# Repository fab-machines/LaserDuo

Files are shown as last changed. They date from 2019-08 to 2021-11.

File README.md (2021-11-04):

<div align="center"><h1 style="font-family: courier;" align="center">LaserDuo</h1></div>

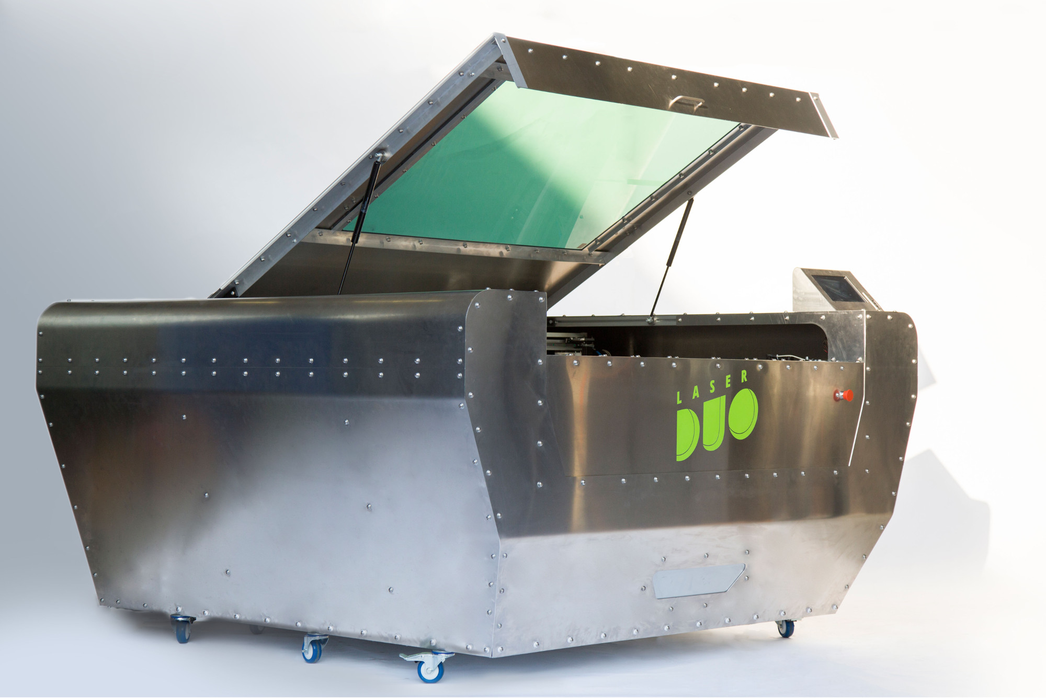
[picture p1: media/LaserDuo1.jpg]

<div align="center"><i>Open Source Dual Laser Cutter</i></div>

Premises
--
We dream in a future of freedom, where open source hardware and [Fab Labs](https://fablabs.io/) enable people to fully understand how to make things they need, and where decentralized local production is customized to impact the surrounding community. Believing that empowering the user with knowledge about how to make machines, LaserDuo wants to give to the world a powerful open source tool, to lasercut (almost) any material. And, together with [BigFDM](https://github.com/fab-machines/BigFDM), this is one of the first steps in developing other machines sharing the same philosophy.

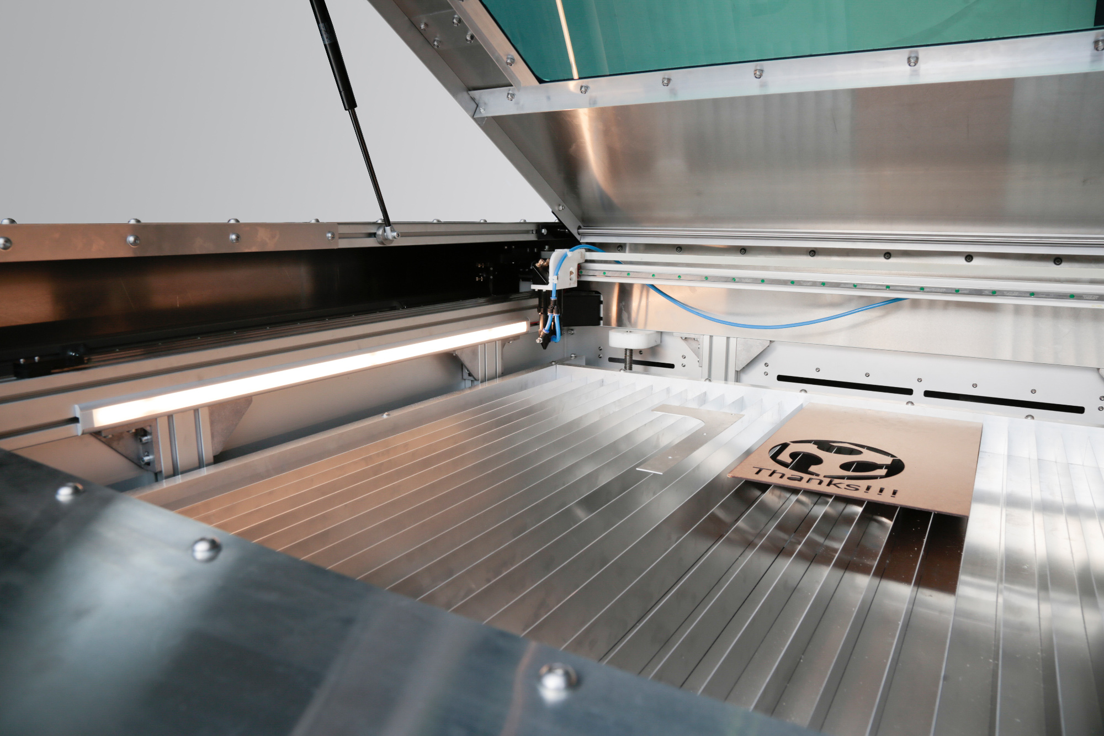
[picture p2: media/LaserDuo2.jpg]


LaserDuo
--
LaserDuo is an open source laser cutter having two different laser sources. Using a 130W CO2 and a 75W YAG lasers, LaserDuo can work with a wide range of materials such as wood and metals.

Taking advantage of what we have learned in [Fab Academy](https://fabacademy.org/), LaserDuo has been developed using standard [Fab Lab equipment](https://docs.google.com/spreadsheets/d/1U-jcBWOJEjBT5A0N84IUubtcHKMEMtndQPLCkZCkVsU/pub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) and [techniques](http://fab.academany.org/2019/schedule.html) plus a membrane press machine to bend the aluminum parts. LaserDuo was developed at [Fab Lab Kamp-Linfort](https://fablab.hochschule-rhein-waal.de/about-us) by Daniele Ingrassia. Reversing the consumer process, where knowledge and building of machines stays inside a black box managed by companies, LaserDuo brings the advantages of an open source development:

- full awareness about how the machine works
- reproducible design
- possibility to customize the machine and/or to build new ones
- built as much as possible with local materials
- local self-fixing and self-production of the machine parts
- community can use and improve the design
- cheap alternative to large scale 3D printers
- use LaserDuo as tool to produce other open source machines

Developed and built in a Fab Lab as multipurpose machine, LaserDuo allows to access the laser cutting technology at lower price in comparison to similar machines available on the market. Especially considering the possibility to work with metals. The open source design allows the user to fix the machine by himself, and to be aware of the process in a way that he can use it to reproduce the machine or parts for it. Being a challenging project from several aspects, such as size of the working area, Z-axis, speed, resolution and the dual laser, it also offers additional features like an integrated PC to control the machine and launch jobs, air assist, solid aluminum bodywork.

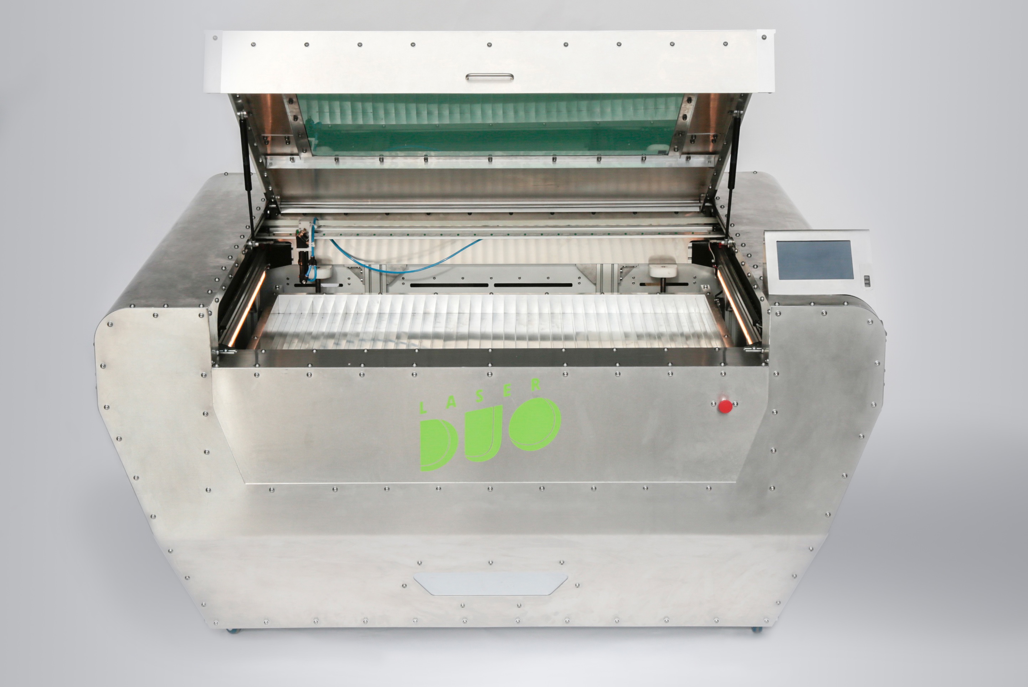
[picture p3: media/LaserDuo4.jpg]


**LaserDuo specifications**:

- **1500mm x 1000mm** cutting area
- **500mm Z axis**
- **dual laser source**
- **130W CO2** laser
- **75W YAG** laser
- **800mm/s** maximum speed
- **Nema 24** stepper motors
- **air assist**
- integrated **tablet** for machine control
- **1000DPI or 0.0254mm** resolution
- open source **satshakit biards** for machine control
- dedicated sealed **exhaust chamber**
- **certified laser protective window**
- **safety features** emergency switch, windows interlock
- **fully enclosed 100% aluminum housing**
- dimensions: 2250mm x 2100mm x 1500mm

Machine design
--
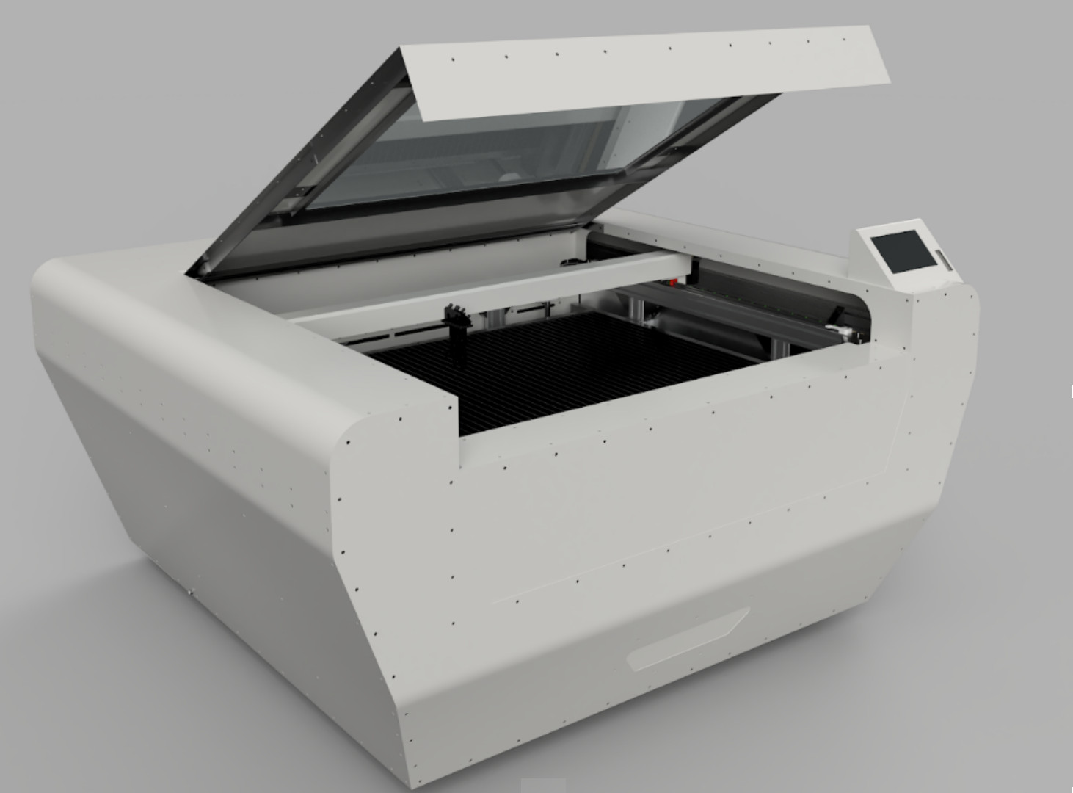
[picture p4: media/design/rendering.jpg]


The overall project has been designed by following a bottom-up approach, where the first step was to make a single machine axis. Every step focused on developing a single machine section, designing and constraining it according to the previous steps and machine features. You can consider this like being almost blind about the next step, until the current one has been assessed as able to work properly. It is therefore for me still astonishing the complete transition to the final machine look, generated by the chaining of the dependencies of several design steps.

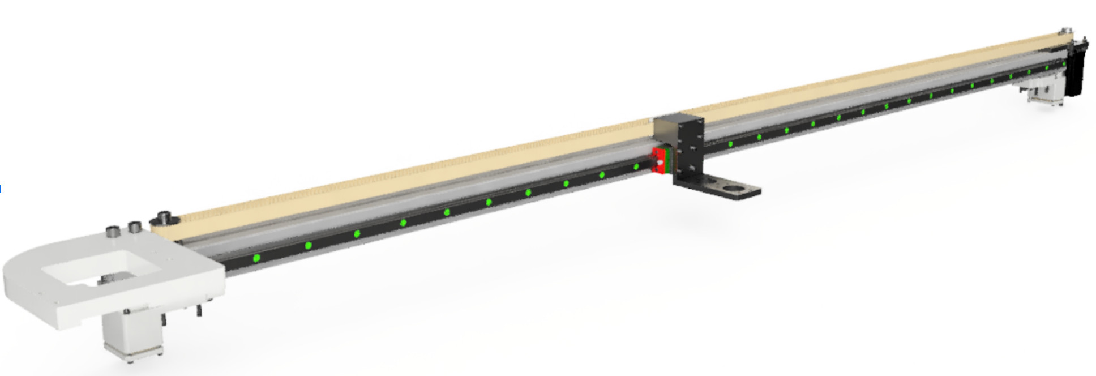
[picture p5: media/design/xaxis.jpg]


X and Y stages
--

As many other laser cutters, also the stages of LaserDuo have been designed to be light and fast. Linear rails together with CNC milled POM and aluminium profiles have been used. To be noticed this step took a lot time, especially during the assembly to ensure the correct squareness of the frame and the perpendicularity of the axis. Both X and Y axis are moved by Nema 24 motors.

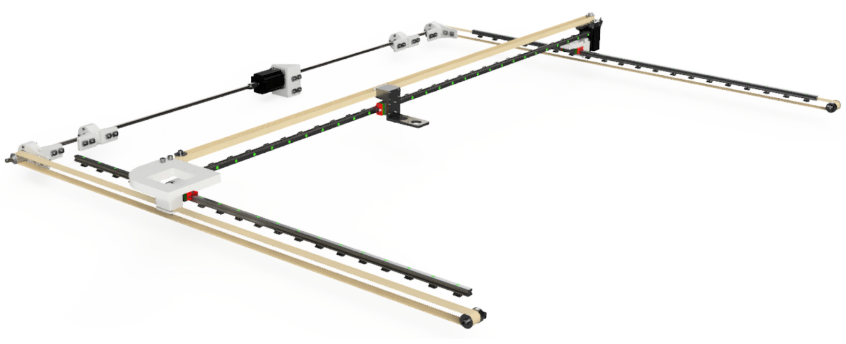
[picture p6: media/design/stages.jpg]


Z Axis
--

I always had something to do with lasers having Z axis, before learning that some chinese laser don’t have it. Therefore for me was quite normal to consider to have it. However I had a long reasoning about the justification of the extra costs vs the possible benefits. Then I had the idea to eventually make a 3D printer as a possible upgrade for LaserDuo, while considering that I still needed to find a solution to properly take the focus by moving the lens up and down. That convinced me to add it. The Z axis consist of 4 lead-screws, supported by ball bearings and moved a closed loop belt. The frame has been designed in a way to fit the Z axis inside and to have the machine high enough to be on wheels.

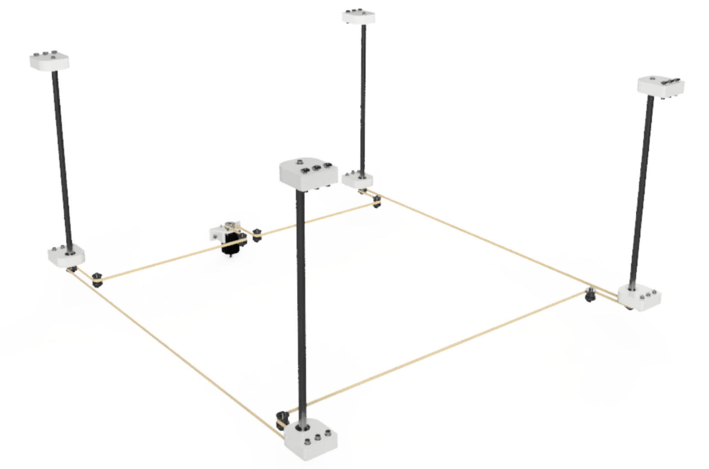
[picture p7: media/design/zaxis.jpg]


Inner enclousure
--

Designed on purpose to shield the laser focusing area and to make the fumes having a certain flow towards the exhaust system, the inner enclosure consists of CNC milled 1.5mm anodized aluminium sheets. There are vents both in the front and the back, allowing fresh air to come from outside, cool the cutting area, and be exhausted through a sealed box.

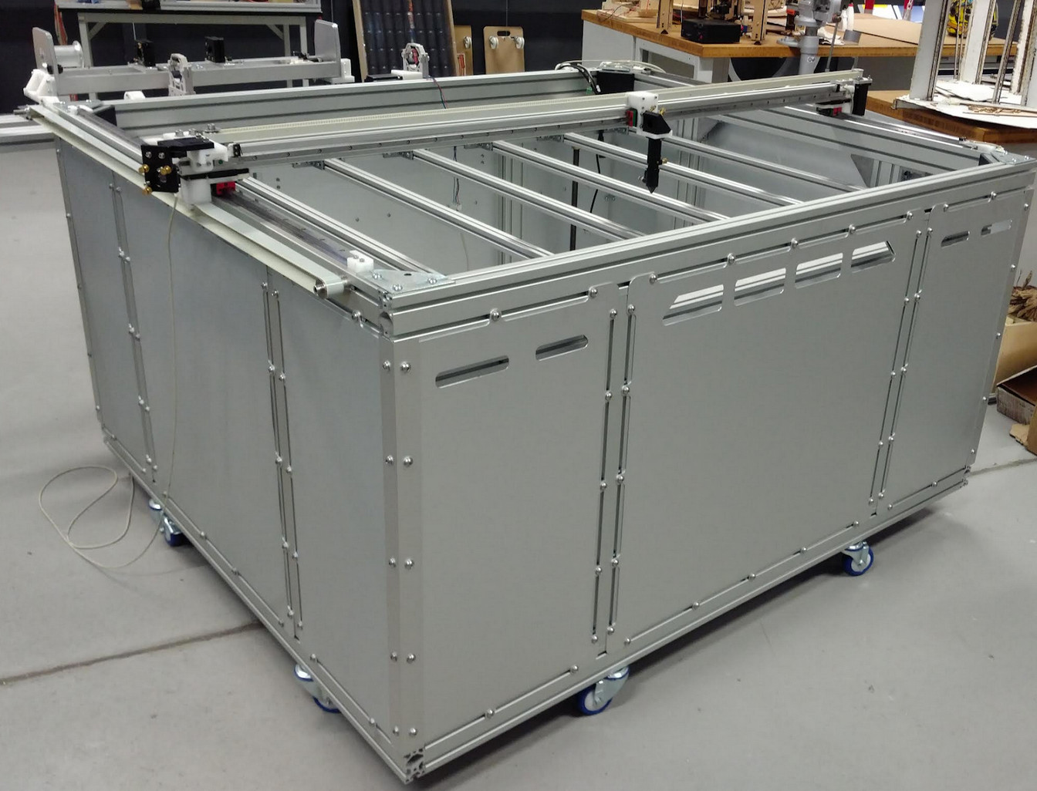
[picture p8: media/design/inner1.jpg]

<br><br><br>
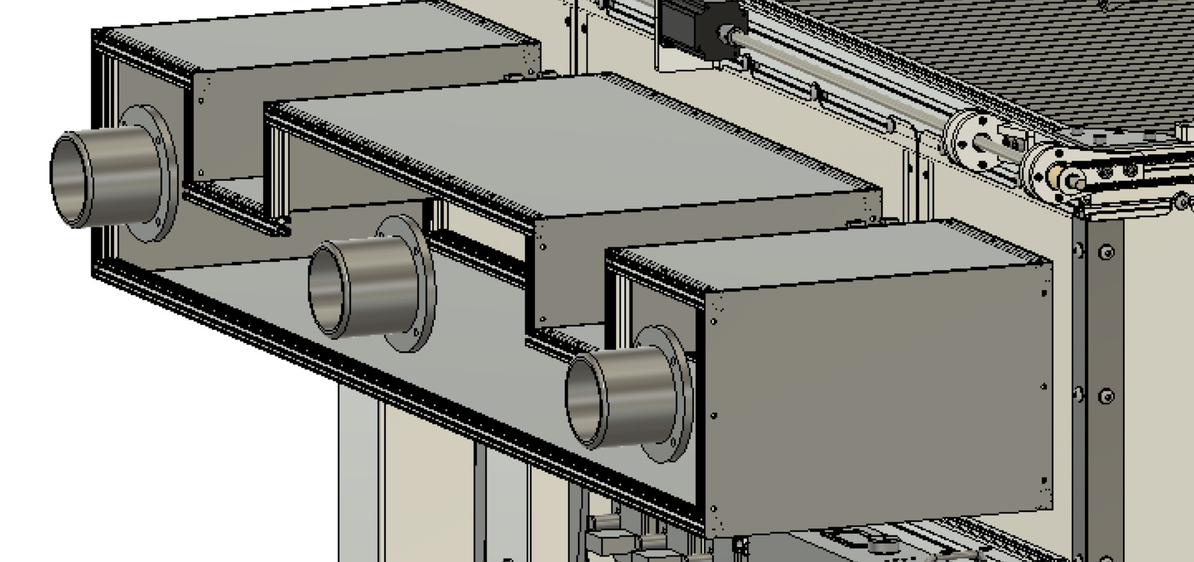
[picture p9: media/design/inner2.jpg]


Housing
--

The housing completely encloses the machine, while keeping 3 exhaust tubes in the back and some ultrathin air intakes. The design uses curves to allow the feet to fit when coming close to the machine, and as well to save material. Laser, exhaust, electronics and optics are located in different areas, accessible by removing a specific panel for maintenance.

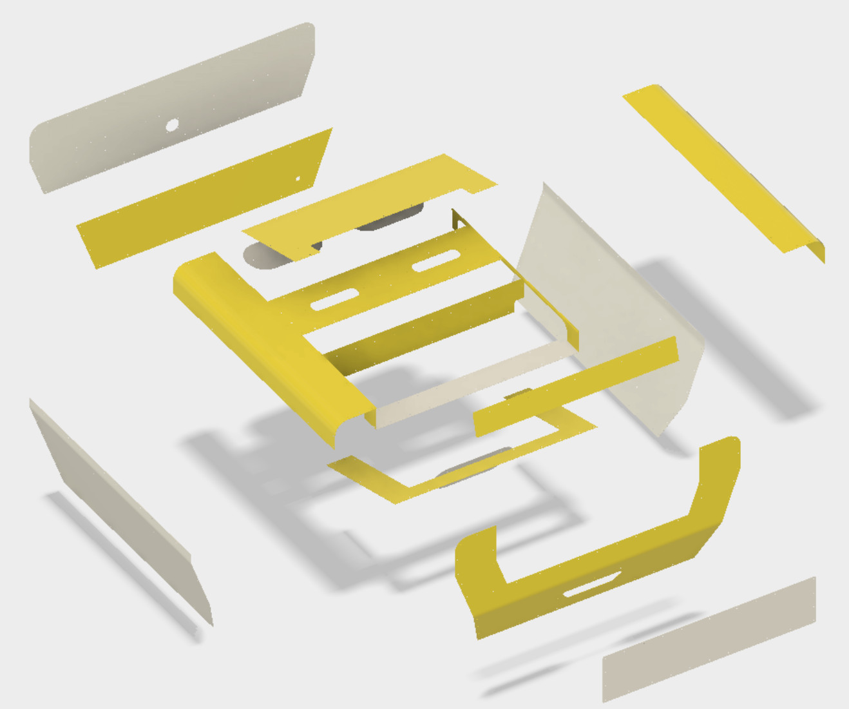
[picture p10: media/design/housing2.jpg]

<br><br><br>
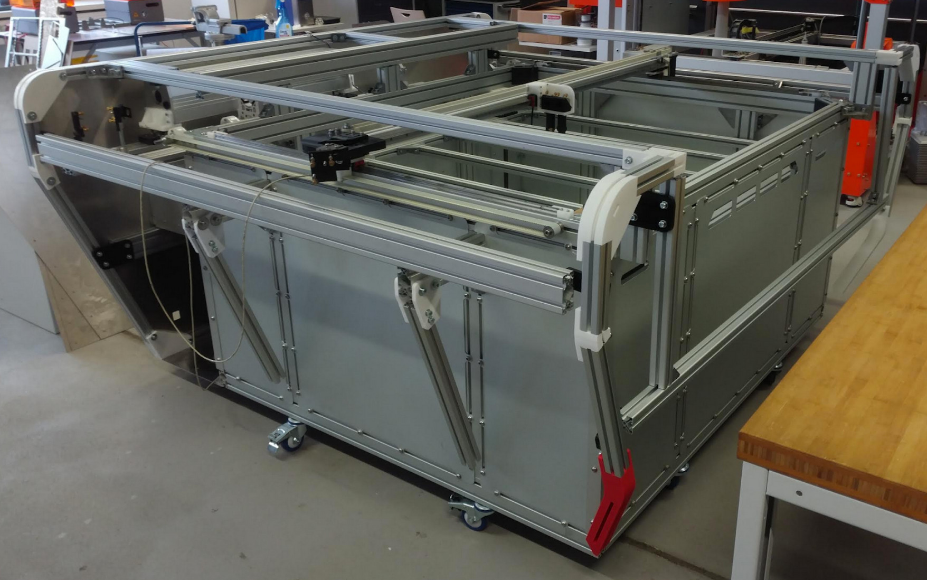
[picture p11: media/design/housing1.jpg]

<br><br><br>
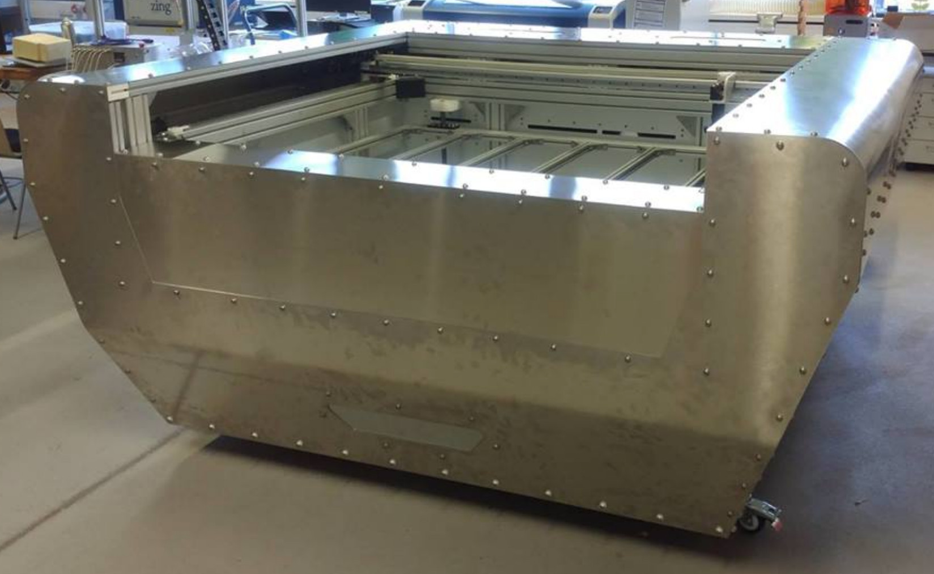
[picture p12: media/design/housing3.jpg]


Electronics
--
The electronics of LaserDuo consists of a set of fabbable electronics, derived from the original **[satshakit](https://github.com/satshakit)** board and **[satstep](https://github.com/satstep)** stepper drivers. Following the used boards and their role in LaserDuo.<br>

**[satshakit-mega](https://github.com/fab-machines/LaserDuo/tree/master/electronics/satshakit-mega)**

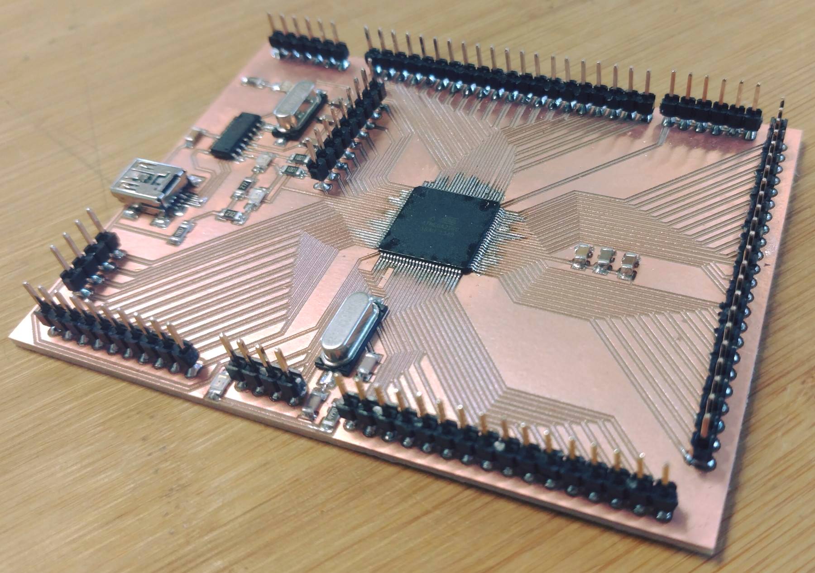
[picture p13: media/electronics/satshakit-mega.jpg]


Based on the [ATMega2560](https://www.microchip.com/wwwproducts/en/ATmega2560), this board provides the necessary microcontroller hardware to manage LaserDuo dual laser logic and additional sensors. Furthermore integrates an USB-to-Serial converter and USB port. Developed as general purpose board, not all the pins will be used. In the future this board will be a custom made solution for LaserDuo. Link to the original [repo](https://github.com/satshakit/satshakit-mega).

---------

**[satshakit-grbl](https://github.com/fab-machines/LaserDuo/tree/master/electronics/satshakit-grbl)**

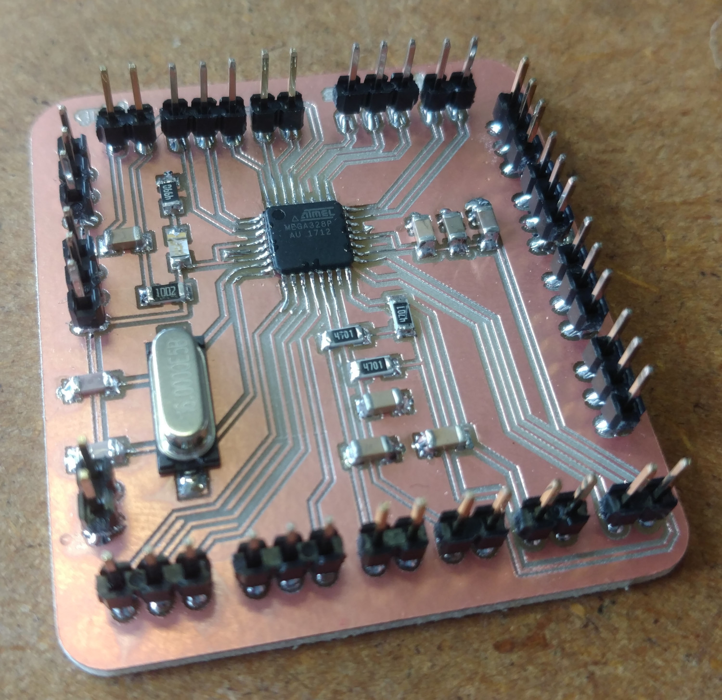
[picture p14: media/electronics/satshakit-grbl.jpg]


Used to run **[GRBL 1.1](https://github.com/gnea/grbl)** in laser mode, satshakit-grbl is based on the ATMega328p and as well integrates nise filtering for the endstops. Link to the original repo [satshakit-grbl](https://github.com/satshakit/satshakit-grbl)

---------

**[satstep6600](https://github.com/fab-machines/LaserDuo/tree/master/electronics/satstep6600)**

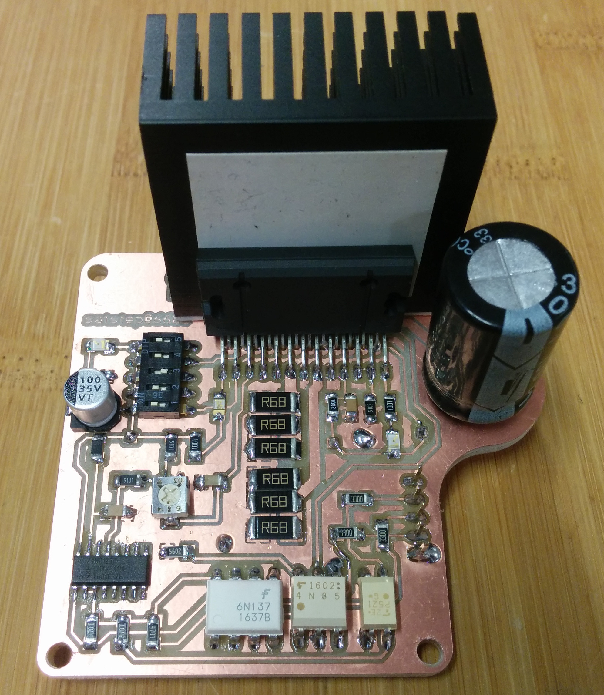
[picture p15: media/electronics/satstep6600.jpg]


Proved to have a robust design by being used in **[LaserDuo](http://laserduo.com/)** for more than a year, the satstep6600 is the stepper driver used to move the NEMA 24. Based on the Toshiba [TB6600HG](http://www.massmind.org/images/massmind/TB6600HG_datasheet.pdf) it can give up to 4.5A per coil to a single motor, whereas the NEMA 24 used will take a maximum of 4A. Link to the original [repo](https://github.com/satstep/satstep6600).

---------

Summary of the needed boards:

- 1 x satshakit-mega
- 1 x satshakit-grbl
- 3 x satstep6600

To power all this electronics, and to control the laser sources the following additional electronics is needed:

- 15A 24V power supply
- CO2 power supply (~40KV)
- YAG power supply

Make your own LaserDuo
--

LaserDuo is made by using a mix of fabricated and ready-made parts. The ready-made parts are selected to be as common/standard as possible, to make the sourcing of them easy in many countries. For both the raw materials needed for the fabricated parts, and the ready-made parts, refer to the Bill-of-Material for details: **[LaserDuo BOM](https://github.com/fab-machines/LaserDuo/raw/master/docs/LaserDuo%20BOM.pdf)**

The fabrication of the parts mainly relays on standard [Fab Lab equipment](https://docs.google.com/spreadsheets/d/1U-jcBWOJEjBT5A0N84IUubtcHKMEMtndQPLCkZCkVsU/pub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) plus a membrane press machine. Below a list of the required tools and machines:

- C02 laser cutter:
 - able to cut 8mm POM
 - needed for POM parts and holders
- large format wood CNC machine:
 - ShopBot or similar, size 2500x1250mm
 - to machine the POM parts (X, Y, Z, axis)
 - to machine the Aluminum parts (inner enclousure, housing)
- 3D printer:
 - a medium sized one (50x50x50cm)
 - to print the inner housing parts 
- Desktop format CNC machine:
 - Roland MDX50/MDX20/SRM20 or similar small machine (as well the cheap chinese ones)
 - to produce the required PCBs
- standard set of tools:
 - spanner key set
 - hex key set
 - DIN 875
 - calipers
 - rulers
 - screwdriver set
 - player set (grabber/cutter etc..)
 - clamps
 - rubber hummers
- membrane press machine
 - to bend the housing parts  

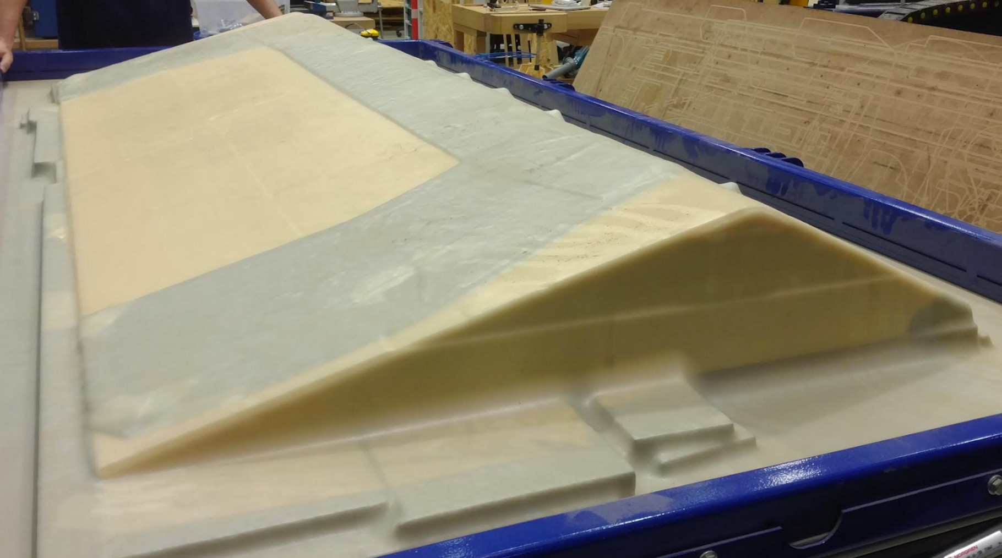
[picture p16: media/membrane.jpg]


Both fabricated and ready-made parts have been modeled inside the **[LaserDuo Fusion 360 3D model](https://github.com/fab-machines/LaserDuo/raw/master/cad/LaserDuo.f3d)**. Using Fusion is possible to export/prepare the parts for production in the following ways:

- right click save as STL, on a body that needs to be 3D printed
- use the built-in Fusion CAM processor for the machined parts
- project on a surface, and then right click export as DXF, for laser cutting
 
For more details about the tools and once you have all the fabricated and ready-made parts parts available, refer to the for step-by-step assembly instructions and tips: **[LaserDuo Building Manual](https://github.com/fab-machines/LaserDuo/raw/master/docs/LaserDuo%20building%20manual.pdf)** 

LaserDuo requires different fabbable PCBs to work. Below the download links for the eagle files that you use to fabricate them:

- **[satshakit-mega schematic](https://raw.githubusercontent.com/fab-machines/LaserDuo/master/electronics/satshakit-mega/satshakit-mega.sch)**, **[satshakit-mega board](https://raw.githubusercontent.com/fab-machines/LaserDuo/master/electronics/satshakit-mega/satshakit-mega.brd)**

- **[satstep6600 schematic](https://github.com/fab-machines/LaserDuo/raw/master/electronics/satstep6600/satstep6600.sch)**, **[satstep6600 board](https://github.com/fab-machines/LaserDuo/raw/master/electronics/satstep6600/satstep6600.brd)**

- **[satshakit-grbl schematic](https://github.com/fab-machines/LaserDuo/raw/master/electronics/satshakit-grbl/satshakit-grbl.sch)**, **[satshakit-grbl board](https://github.com/fab-machines/LaserDuo/raw/master/electronics/satshakit-grbl/satshakit-grbl.brd)**

Media
--
**LaserDuo Videos**

<a href="http://www.youtube.com/watch?feature=player_embedded&v=9PNHiuEieJk
" target="_blank"></a>

<a href="http://www.youtube.com/watch?feature=player_embedded&v=rJKmr8BXJXA
" target="_blank"></a>

<a href="http://www.youtube.com/watch?feature=player_embedded&v=EAzdC5dfosA
" target="_blank"></a>

**How to Make LaserDuo: Hamburg Workshop at [Open Lab](http://openlab-hamburg.de/startpage/)**

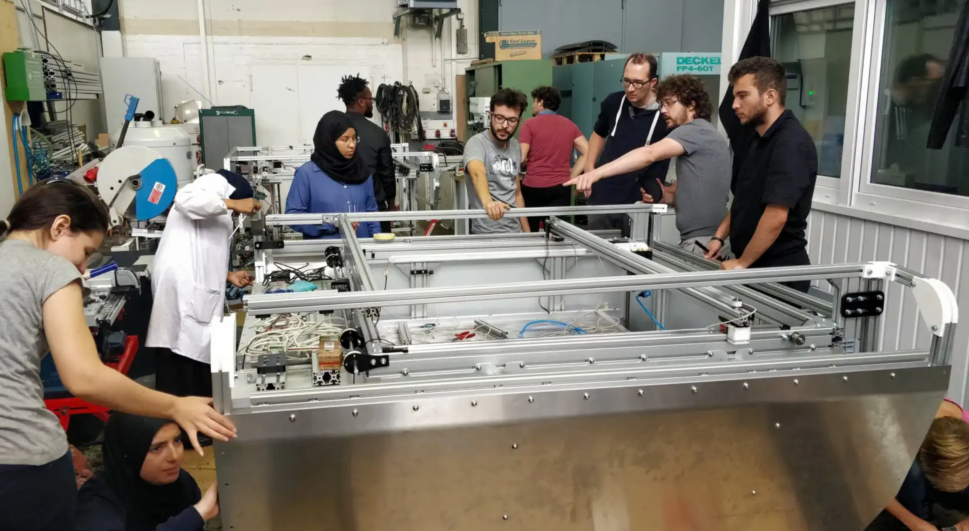
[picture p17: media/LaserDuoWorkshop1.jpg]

<br><br><br>
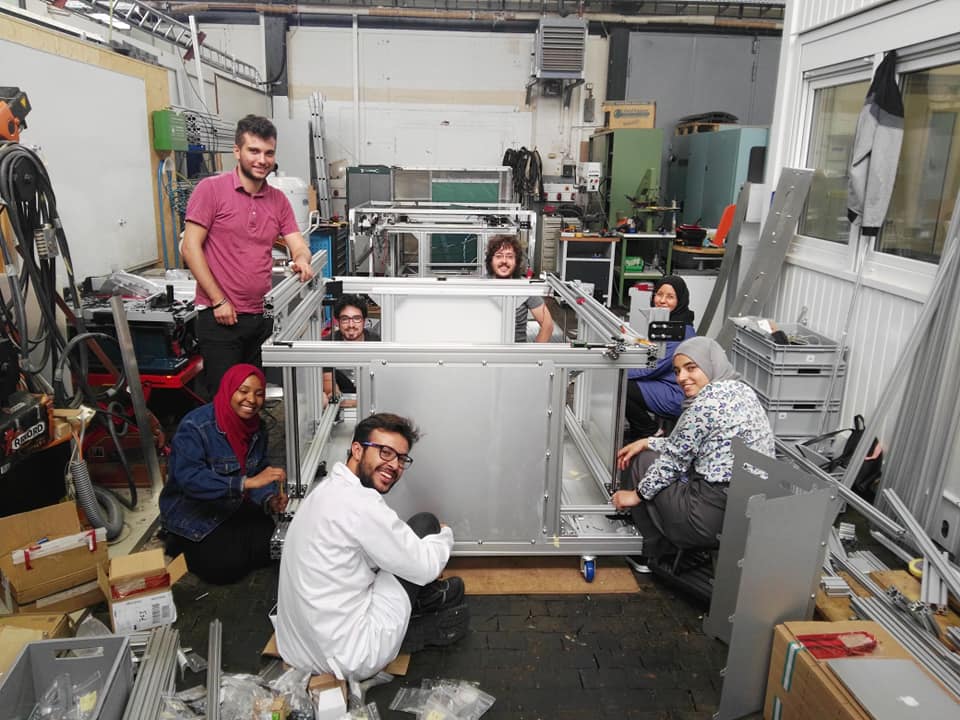
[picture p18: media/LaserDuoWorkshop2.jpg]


**LaserDuo pictures**

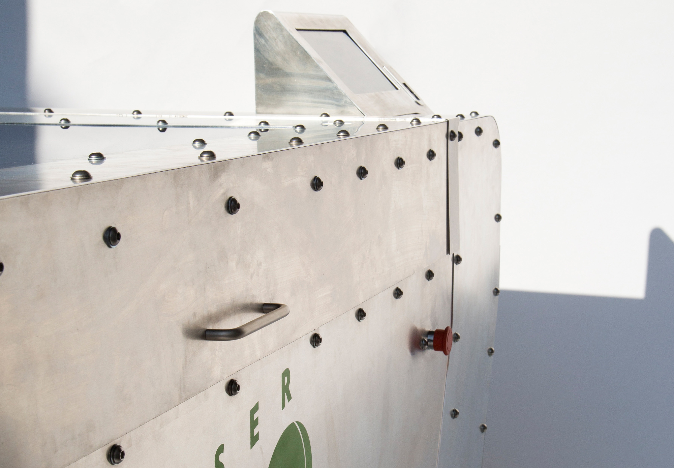
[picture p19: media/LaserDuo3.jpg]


Author
--

The author of BigFDM is:

- **Daniele Ingrassia, daniele@inmachines.net**
- **[InMachines Ingrassia GmbH](https://www.inmachines.net/)**

Donations
--

Our dream is to have impact by making **open source machines digitally available and locally produced anywhere in world**. We plan to open a dedicated Fab Lab to foster open machine building and digital fabrication research. Practically several tasks and many expensens have to be sustained to give this dream the chance to have a future. Such as the renting of a proper space, the making/purchasing of proper equipment, the sustainability of our work and lifes. If you share this mindset and BigFDM is useful to you, please help us to make this dream a reality by donating your support:



Acknowledgements
--

**Thanks:**<br>
<br>
**[Fablab Kamp-Lintfort](https://fablab.hochschule-rhein-waal.de/)**<br />
Hochschule Rhein-Waal<br/>
Friedrich-Heinrich-Allee 25<br/>
47475 Kamp-Lintfort - Germany<br/>
[https://fablab.hochschule-rhein-waal.de/about-us](https://fablab.hochschule-rhein-waal.de/about-us)<br/>
[fablab@hochschule-rhein-waal.de](fablab@hochschule-rhein-waal.de)

Technical Help by **[Ahmed B. Abdellatif](http://archive.fabacademy.org/fabacademy2017/fablabkamplintfort/students/391/index.html)**<br/>
Logo Design by **Jana-Lina Berkenbusch**<br/>
Photographs by **Christian Spieß**<br/>
Website development by **Emir Rustamov**<br/>

****

License
-- 
LaserDuo, its hardware design, CAD, BOM, settings and relative files are are released under the following open source license:

- CERN Open Hardware Licence Version 2 Weakly Reciprocal - **[CERN-OHL-W](LICENSE_CERN_OHL_W_V2.txt)**

Note
--

This documentation will be continuously improved as soon there are updates and/or improvements on the machine.

Disclaimer  
--

<div class="align-justify">
This hardware/software is provided "as is", and you use the hardware/software at your own risk. Under no circumstances shall any author be liable for direct, indirect, special, incidental, or consequential damages resulting from the use, misuse, or inability to use this hardware/software, even if the authors have been advised of the possibility of such damages.</div>

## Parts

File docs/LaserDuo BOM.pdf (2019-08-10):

NOTE: all the costs are in euro, and they include VAT, shipping costs and/or eventually importing taxes for Germany. The costs are approximate and can be subject to changes due to variations of currency exchange rates, quotes from the companies and market availability at the moment of ordering.

Item | Description | Amount | Vendor | Cost per unit | Total cost: | Note
ZS-1450 laser tube | 100W C02 laser source | 1 | EFR Laser | 284€ | 355€ | total cost is with importing taxes included
ES-100 power adapter | C02 power supply | 1 | EFR Laser | 130€ | 162€ | total cost is with importing taxes included
75W DPL-75 laser module | 75W Yag laser source | 1 | Super Laser | 700€ | 875€ | total cost is with importing taxes included
I20N DPL power adapter | Yag power supply | 1 | Super Laser | 150€ | 190€ | total cost is with importing taxes included
CW5200 Double Head | Water Chiller | 1 | Teyuchiller | 400€ | 500€ | total cost is with importing taxes included
QSD7527 Q-Driver | Q-Switch power adapter | 1 | CETC | 400€ | 500€ | total cost is with importing taxes included
QSGSU-5 Q-Switch | Yag Q-Switch | 1 | CETC | 300€ | 375€ | total cost is with importing taxes included
HGR15 | Linear guides for X,Y | 5mt | Hiwin | 50€ | 250€
T20 lead screws and bras nuts | 20mm pitch lead screws and nuts for the Z axis | 4 x 1.5mt,4 x nuts | Dold-Mechatronics | 50€ | 200€
Pulleys T5 20mm, 16mm and 10mm | Pulleys for X, Y, Z axis | 2x20mm,1x16mm,1x10mm | Generic | 15€ | 60€
Belt T5 20mm, 16mm and 10mm | T5 belts for X,Y,Z axis | 20mm, 16mm, 10mm,15mt | Generic | - | 200€
Nema24 stepper motors | Motors for the X,Y,Z axis | 3 | Generic | 30€ | 90€
satshakit-mega | Main controller | 1 | open source electronics | 15€ | 15€
satshakit-grbl | Secondary controller | 2 | open source electronics | 10€ | 20€
satstep6600 | Stepper driver | 3 | open source electronics | 15€ | 45€
24V 15A power supply | Power supply for the steppers | 1 | Generic | 30€ | 30€
20x20, 40x40, 40x80, 30x30, 30x60 Bosch, L profiles | Aluminium profiles for the frame and the housing | approx 50mt summing all the sizes | Generic | 1,800€ | 1,800€
DIN 912, ISO 7380, DIN 125, DIN 985, DIN 934, Nut8 M4, Nut8 M8, Nut5 M5, Connectors | Screws, nuts and connectors. | - | Generic | - | 400€
608, 628, 638 | Ball bearings for the X,Y,Z axis | 40 | Generic | 2€ | 80€
PLA | PLA for the printed parts | 10Kg | Generic | 14€ | 140€
POM/Derlin | CNC machines POM for mechanical parts | about 70Kg | Generic | 5€ | 350€
Laser optics, head, laser path, lenses | Laser accessory for C02 and Yag | - | Generic | 250€ | 315€ | total cost is with importing taxes included
P1P12 Filter 6mm | Certified laser protective window | 1200mmx900mm | Laservision | 1,800€ | 1,800€
1.5mm anodized aluminium sheets | Aluminium sheets for the internal enclosure | Approx 10 sqm | Generic | 35€ | 350€
1.5mm aluminium sheets | Aluminium sheets for the external enclosure | Approx 16sqm | Generic | 35€ | 560€
Hi10 tablet | Tablet for controlling the machine | 1 | Chuwi | 150€ | 150€
Emergency switches, endstop switches, main switch | Switches for different purposes | 10 | Generic | - | 50€
2X1, 4X1, power cables, signal cables | Shielded electrical cables | 50mt | Generic | - | 100€
Led lights 20W | Wheels to move the machine Plastic water and ir tubes Led lights for the interior | 20mt 20 8 | Generic Generic Generic | 10€ 2€ - | 40€ Water and air tubes 50€ Wheels 100KG M8 Bosch 80€
Air compressor 6 bar 4 cylinders | Air compressor for the air assist | 1 | Generic | 130€ | 130€
End mills 6mm and 3mm, 25mm drill bit, zip ties, shrinking tubes, electrical tape, special imbiss key, grabber | Consumables, special tools required to build the machine | - | Generic | - | 100€
| | | | Total: | 10,362€

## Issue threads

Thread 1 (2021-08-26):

software

lianzaozi, 2021-08-26:
What kind of software is used to control the laser cutting machine?

satshas, 2021-08-30:
Hello @lianzaozi,

the following software is used:

- grbl, https://github.com/gnea/grbl,  on the satshakit-grbl
- UGSG Platform, https://winder.github.io/ugs_website/guide/platform/, to operate the machine
-  Visicut,, https://winder.github.io/ugs_website/guide/platform/, to generate the GCode (use grbl driver)

let me know if you need more information

Closed 2021-08-30.

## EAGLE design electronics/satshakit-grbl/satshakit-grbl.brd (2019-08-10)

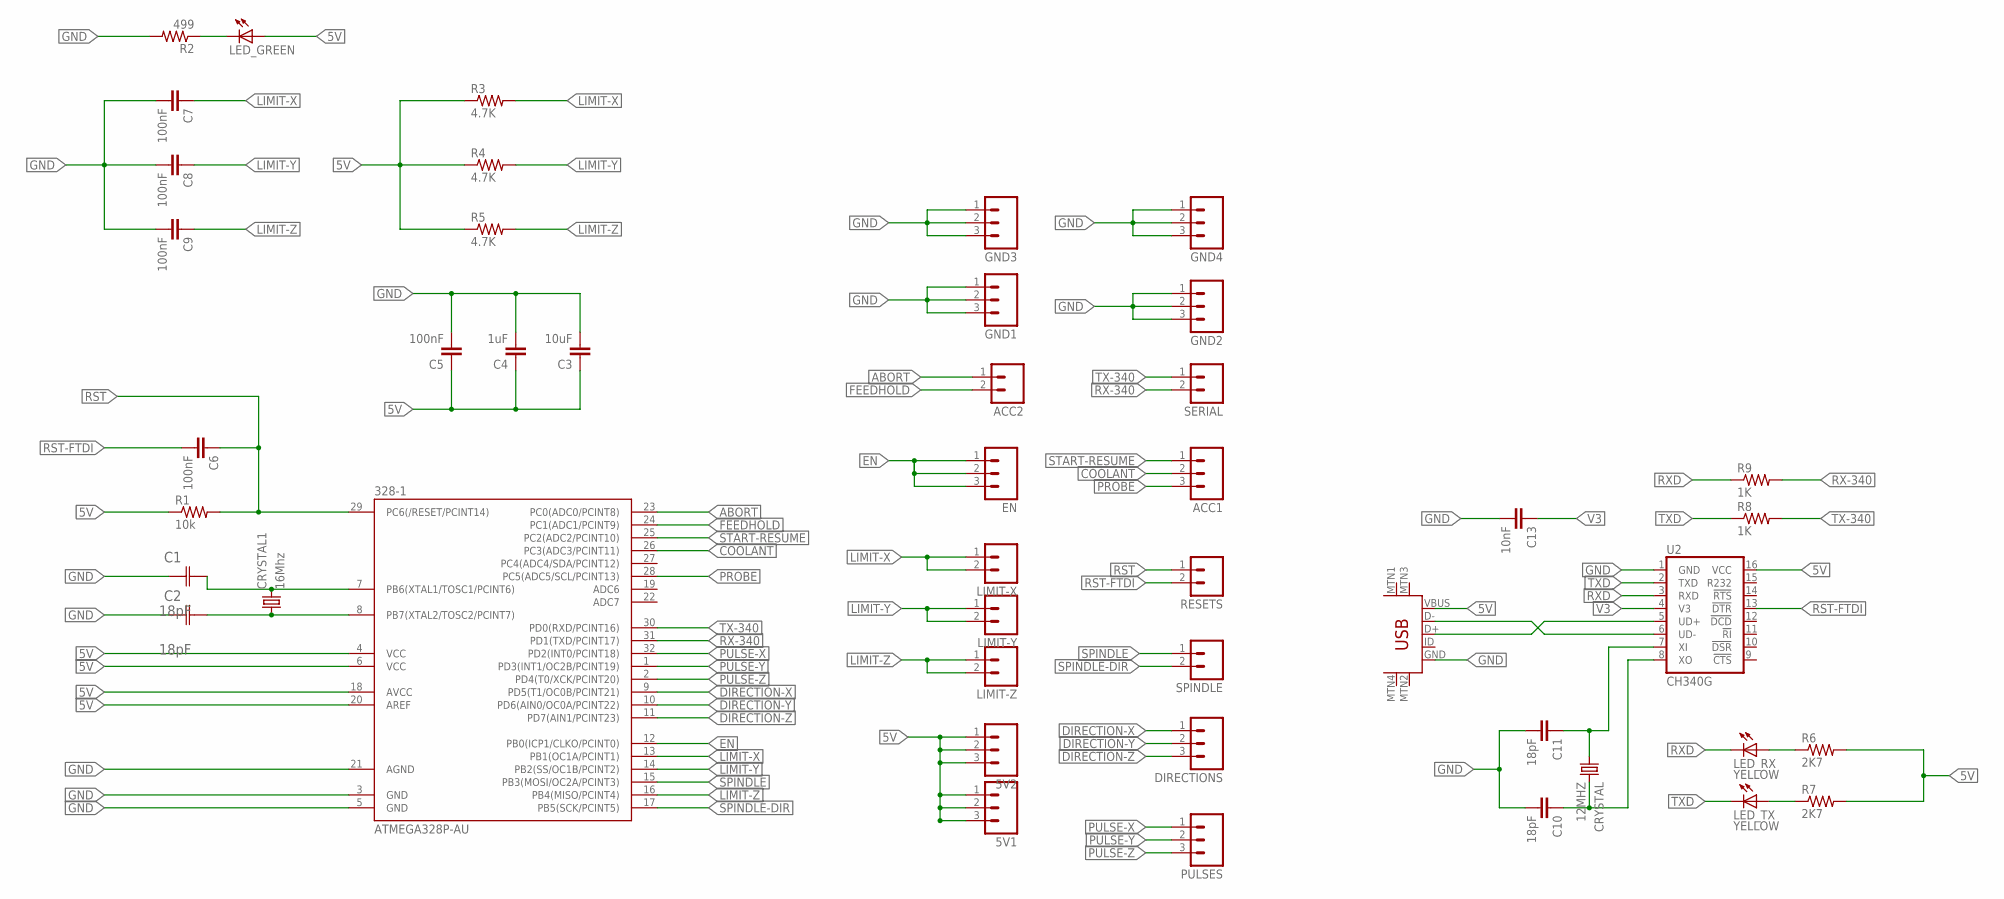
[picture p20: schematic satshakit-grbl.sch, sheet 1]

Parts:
5V1, 5V2: M03; 03P
328-1: ATMEGA328P-AU; TQFP32-08
ACC1: M03; 03P
ACC2: M02; 02P
C1, C2: 18pF; CAPC3216X178N
C3: 10uF; 1206
C4: 1uF; 1206
C5, C6, C7, C8, C9: 100nF; 1206
C10, C11: 18pF; 1206
C13: 10nF; 1206
CRYSTAL: 12MHZ; CSM-7X-DU
CRYSTAL1: 16Mhz; CSM-7X-DU
DIRECTIONS: M03; 03P
EN: M03; 03P
GND1, GND2, GND3, GND4: M03; 03P
LED_GREEN: LED1206; 1206
LED_RX: YELLOW; LED1206
LED_TX: YELLOW; LED1206
LIMIT-X: M02; 02P
LIMIT-Y: M02; 02P
LIMIT-Z: M02; 02P
PULSES: M03; 03P
R1: 10k; 1206
R2: 499; 1206
R3, R4, R5: 4.7K; 1206
R6, R7: 2K7; R1206
R8, R9: 1K; R1206
RESETS: M02; 02P
SERIAL: M02; 02P
SPINDLE: M02; 02P
U2: CH340G; SO016
U$7: USB-MINIB-5PIN; USB-MINIB

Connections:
5V: 5V1.1, 5V1.2, 5V1.3, 5V2.1, 5V2.2, 5V2.3, 328-1.4 (VCC), 328-1.6 (VCC), 328-1.18 (AVCC), 328-1.20 (AREF), C3.1, C4.1, C5.1, LED_GREEN.1 (A), R1.1, R3.1, R4.1, R5.1, R6.2, R7.2, U2.16 (VCC), U$7.VBUS
ABORT: 328-1.23 (PC0(ADC0/PCINT8)), ACC2.1
COOLANT: 328-1.26 (PC3(ADC3/PCINT11)), ACC1.2
DIRECTION-X: 328-1.9 (PD5(T1/OC0B/PCINT21)), DIRECTIONS.1
DIRECTION-Y: 328-1.10 (PD6(AIN0/OC0A/PCINT22)), DIRECTIONS.2
DIRECTION-Z: 328-1.11 (PD7(AIN1/PCINT23)), DIRECTIONS.3
EN: 328-1.12 (PB0(ICP1/CLKO/PCINT0)), EN.1, EN.2, EN.3
FEEDHOLD: 328-1.24 (PC1(ADC1/PCINT9)), ACC2.2
GND: 328-1.3 (GND), 328-1.5 (GND), 328-1.21 (AGND), C1.1 (C1), C2.1 (C1), C3.2, C4.2, C5.2, C7.2, C8.2, C9.2, C10.2, C11.2, C13.2, GND1.1, GND1.2, GND1.3, GND2.1, GND2.2, GND2.3, GND3.1, GND3.2, GND3.3, GND4.1, GND4.2, GND4.3, R2.2, U2.1 (GND), U$7.GND
LIMIT-X: 328-1.13 (PB1(OC1A/PCINT1)), C7.1, LIMIT-X.1, LIMIT-X.2, R3.2
LIMIT-Y: 328-1.14 (PB2(SS/OC1B/PCINT2)), C8.1, LIMIT-Y.1, LIMIT-Y.2, R4.2
LIMIT-Z: 328-1.16 (PB4(MISO/PCINT4)), C9.1, LIMIT-Z.1, LIMIT-Z.2, R5.2
unnamed: U2.5 (UD+), U$7.D+
unnamed: 328-1.7 (PB6(XTAL1/TOSC1/PCINT6)), C1.2 (C2), CRYSTAL1.2
unnamed: U2.6 (UD-), U$7.D-
unnamed: LED_RX.1 (A), R6.1
unnamed: LED_TX.1 (A), R7.1
unnamed: 328-1.8 (PB7(XTAL2/TOSC2/PCINT7)), C2.2 (C2), CRYSTAL1.1
unnamed: LED_GREEN.2 (C), R2.1
OSC_IN: C10.1, CRYSTAL.2, U2.8 (XO)
OSC_OUT: C11.1, CRYSTAL.1, U2.7 (XI)
PROBE: 328-1.28 (PC5(ADC5/SCL/PCINT13)), ACC1.3
PULSE-X: 328-1.32 (PD2(INT0/PCINT18)), PULSES.1
PULSE-Y: 328-1.1 (PD3(INT1/OC2B/PCINT19)), PULSES.2
PULSE-Z: 328-1.2 (PD4(T0/XCK/PCINT20)), PULSES.3
RST: 328-1.29 (PC6(/RESET/PCINT14)), C6.1, R1.2, RESETS.1
RST-FTDI: C6.2, RESETS.2, U2.13 (!DTR)
RX-340: 328-1.31 (PD1(TXD/PCINT17)), R9.2, SERIAL.2
RXD: LED_RX.2 (C), R9.1, U2.3 (RXD)
SPINDLE: 328-1.15 (PB3(MOSI/OC2A/PCINT3)), SPINDLE.1
SPINDLE-DIR: 328-1.17 (PB5(SCK/PCINT5)), SPINDLE.2
START-RESUME: 328-1.25 (PC2(ADC2/PCINT10)), ACC1.1
TX-340: 328-1.30 (PD0(RXD/PCINT16)), R8.2, SERIAL.1
TXD: LED_TX.2 (C), R8.1, U2.2 (TXD)
V3: C13.1, U2.4 (V3)

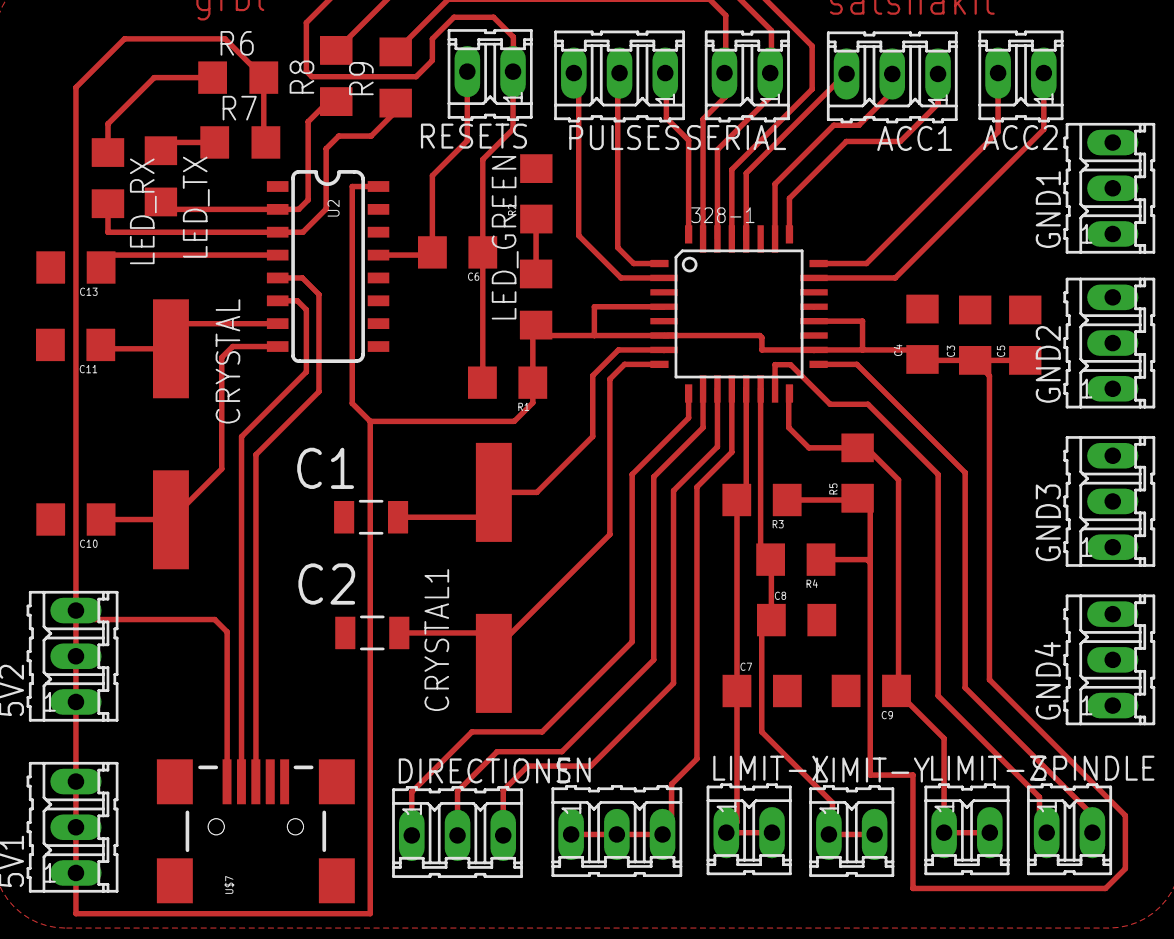
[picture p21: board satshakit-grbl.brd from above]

Board: 2 copper layers, 46 parts (0 on the bottom side), 35 nets.

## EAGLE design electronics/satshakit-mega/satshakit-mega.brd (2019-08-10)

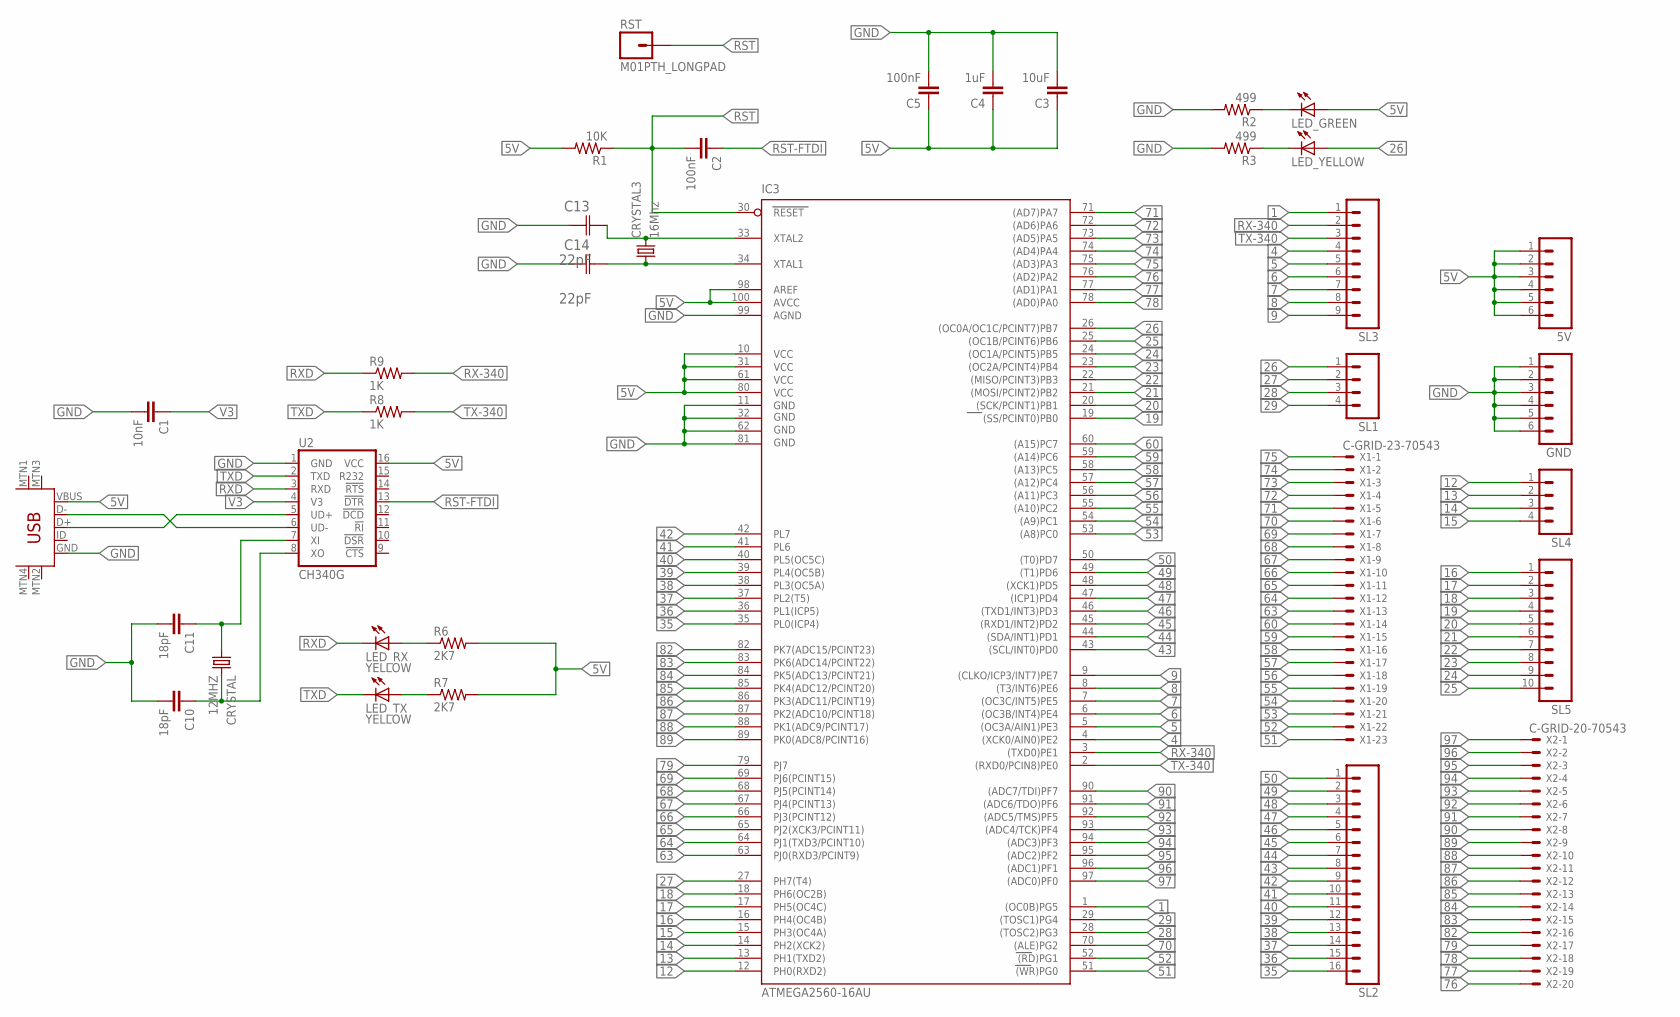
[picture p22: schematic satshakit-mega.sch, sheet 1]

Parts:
5V: M06; 06P
C1: 10nF; 1206
C2, C5: 100nF; 1206
C3: 10uF; 1206
C4: 1uF; 1206
C10, C11: 18pF; 1206
C13, C14: 22pF; CAPC3216X178N
CRYSTAL: 12MHZ; CSM-7X-DU
CRYSTAL3: 16Mhz; CSM-7X-DU
GND: M06; 06P
IC3: ATMEGA2560-16AU; TQFP100
LED_GREEN: LED1206; 1206
LED_RX: YELLOW; LED1206
LED_TX: YELLOW; LED1206
LED_YELLOW: LED1206; 1206
R1: 10K; R1206
R2, R3: 499; 1206
R6, R7: 2K7; R1206
R8, R9: 1K; R1206
RST: M01PTH_LONGPAD; 1X01_LONGPAD
SL1, SL4: M04; 04P
SL2: M16; 16P
SL3: M09; 09P
SL5: M10; 10P
U2: CH340G; SO016
U$7: USB-MINIB-5PIN; USB-MINIB
X1: C-GRID-23-70543; 70543-23
X2: C-GRID-20-70543; 70543-20

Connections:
1: IC3.1 ((OC0B)PG5), SL3.1
4: IC3.4 ((XCK0/AIN0)PE2), SL3.4
5: IC3.5 ((OC3A/AIN1)PE3), SL3.5
5V: 5V.1, 5V.2, 5V.3, 5V.4, 5V.5, 5V.6, C3.1, C4.1, C5.1, IC3.10 (VCC), IC3.31 (VCC1), IC3.61 (VCC2), IC3.80 (VCC3), IC3.98 (AREF), IC3.100 (AVCC), LED_GREEN.1 (A), R1.2, R6.2, R7.2, U2.16 (VCC), U$7.VBUS
6: IC3.6 ((OC3B/INT4)PE4), SL3.6
7: IC3.7 ((OC3C/INT5)PE5), SL3.7
8: IC3.8 ((T3/INT6)PE6), SL3.8
9: IC3.9 ((CLKO/ICP3/INT7)PE7), SL3.9
12: IC3.12 (PH0(RXD2)), SL4.1
13: IC3.13 (PH1(TXD2)), SL4.2
14: IC3.14 (PH2(XCK2)), SL4.3
15: IC3.15 (PH3(OC4A)), SL4.4
16: IC3.16 (PH4(OC4B)), SL5.1
17: IC3.17 (PH5(OC4C)), SL5.2
18: IC3.18 (PH6(OC2B)), SL5.3
19: IC3.19 ((SS/PCINT0)PB0), SL5.4
20: IC3.20 ((SCK/PCINT1)PB1), SL5.5
21: IC3.21 ((MOSI/PCINT2)PB2), SL5.6
22: IC3.22 ((MISO/PCINT3)PB3), SL5.7
23: IC3.23 ((OC2A/PCINT4)PB4), SL5.8
24: IC3.24 ((OC1A/PCINT5)PB5), SL5.9
25: IC3.25 ((OC1B/PCINT6)PB6), SL5.10
26: IC3.26 ((OC0A/OC1C/PCINT7)PB7), LED_YELLOW.1 (A), SL1.1
27: IC3.27 (PH7(T4)), SL1.2
28: IC3.28 ((TOSC2)PG3), SL1.3
29: IC3.29 ((TOSC1)PG4), SL1.4
35: IC3.35 (PL0(ICP4)), SL2.16
36: IC3.36 (PL1(ICP5)), SL2.15
37: IC3.37 (PL2(T5)), SL2.14
38: IC3.38 (PL3(OC5A)), SL2.13
39: IC3.39 (PL4(OC5B)), SL2.12
40: IC3.40 (PL5(OC5C)), SL2.11
41: IC3.41 (PL6), SL2.10
42: IC3.42 (PL7), SL2.9
43: IC3.43 ((SCL/INT0)PD0), SL2.8
44: IC3.44 ((SDA/INT1)PD1), SL2.7
45: IC3.45 ((RXD1/INT2)PD2), SL2.6
46: IC3.46 ((TXD1/INT3)PD3), SL2.5
47: IC3.47 ((ICP1)PD4), SL2.4
48: IC3.48 ((XCK1)PD5), SL2.3
49: IC3.49 ((T1)PD6), SL2.2
50: IC3.50 ((T0)PD7), SL2.1
51: IC3.51 ((WR)PG0), X1.23
52: IC3.52 ((RD)PG1), X1.22
53: IC3.53 ((A8)PC0), X1.21
54: IC3.54 ((A9)PC1), X1.20
55: IC3.55 ((A10)PC2), X1.19
56: IC3.56 ((A11)PC3), X1.18
57: IC3.57 ((A12)PC4), X1.17
58: IC3.58 ((A13)PC5), X1.16
59: IC3.59 ((A14)PC6), X1.15
60: IC3.60 ((A15)PC7), X1.14
63: IC3.63 (PJ0(RXD3/PCINT9)), X1.13
64: IC3.64 (PJ1(TXD3/PCINT10)), X1.12
65: IC3.65 (PJ2(XCK3/PCINT11)), X1.11
66: IC3.66 (PJ3(PCINT12)), X1.10
67: IC3.67 (PJ4(PCINT13)), X1.9
68: IC3.68 (PJ5(PCINT14)), X1.8
69: IC3.69 (PJ6(PCINT15)), X1.7
70: IC3.70 ((ALE)PG2), X1.6
71: IC3.71 ((AD7)PA7), X1.5
72: IC3.72 ((AD6)PA6), X1.4
73: IC3.73 ((AD5)PA5), X1.3
74: IC3.74 ((AD4)PA4), X1.2
75: IC3.75 ((AD3)PA3), X1.1
76: IC3.76 ((AD2)PA2), X2.20
77: IC3.77 ((AD1)PA1), X2.19
78: IC3.78 ((AD0)PA0), X2.18
79: IC3.79 (PJ7), X2.17
82: IC3.82 (PK7(ADC15/PCINT23)), X2.16
83: IC3.83 (PK6(ADC14/PCINT22)), X2.15
84: IC3.84 (PK5(ADC13/PCINT21)), X2.14
85: IC3.85 (PK4(ADC12/PCINT20)), X2.13
86: IC3.86 (PK3(ADC11/PCINT19)), X2.12
87: IC3.87 (PK2(ADC10/PCINT18)), X2.11
88: IC3.88 (PK1(ADC9/PCINT17)), X2.10
89: IC3.89 (PK0(ADC8/PCINT16)), X2.9
90: IC3.90 ((ADC7/TDI)PF7), X2.8
91: IC3.91 ((ADC6/TDO)PF6), X2.7
92: IC3.92 ((ADC5/TMS)PF5), X2.6
93: IC3.93 ((ADC4/TCK)PF4), X2.5
94: IC3.94 ((ADC3)PF3), X2.4
95: IC3.95 ((ADC2)PF2), X2.3
96: IC3.96 ((ADC1)PF1), X2.2
97: IC3.97 ((ADC0)PF0), X2.1
GND: C1.2, C3.2, C4.2, C5.2, C10.2, C11.2, C13.1 (C1), C14.1 (C1), GND.1, GND.2, GND.3, GND.4, GND.5, GND.6, IC3.11 (GND), IC3.32 (GND1), IC3.62 (GND2), IC3.81 (GND3), IC3.99 (AGND), R2.2, R3.2, U2.1 (GND), U$7.GND
unnamed: U2.5 (UD+), U$7.D+
unnamed: LED_RX.1 (A), R6.1
unnamed: U2.6 (UD-), U$7.D-
unnamed: C14.2 (C2), CRYSTAL3.1, IC3.34 (XTAL1)
unnamed: C13.2 (C2), CRYSTAL3.2, IC3.33 (XTAL2)
unnamed: LED_YELLOW.2 (C), R3.1
unnamed: LED_TX.1 (A), R7.1
unnamed: LED_GREEN.2 (C), R2.1
OSC_IN: C10.1, CRYSTAL.2, U2.8 (XO)
OSC_OUT: C11.1, CRYSTAL.1, U2.7 (XI)
RST: C2.2, IC3.30 (RESET), R1.1, RST.1
RST-FTDI: C2.1, U2.13 (!DTR)
RX-340: IC3.3 ((TXD0)PE1), R9.2, SL3.2
RXD: LED_RX.2 (C), R9.1, U2.3 (RXD)
TX-340: IC3.2 ((RXD0/PCIN8)PE0), R8.2, SL3.3
TXD: LED_TX.2 (C), R8.1, U2.2 (TXD)
V3: C1.1, U2.4 (V3)

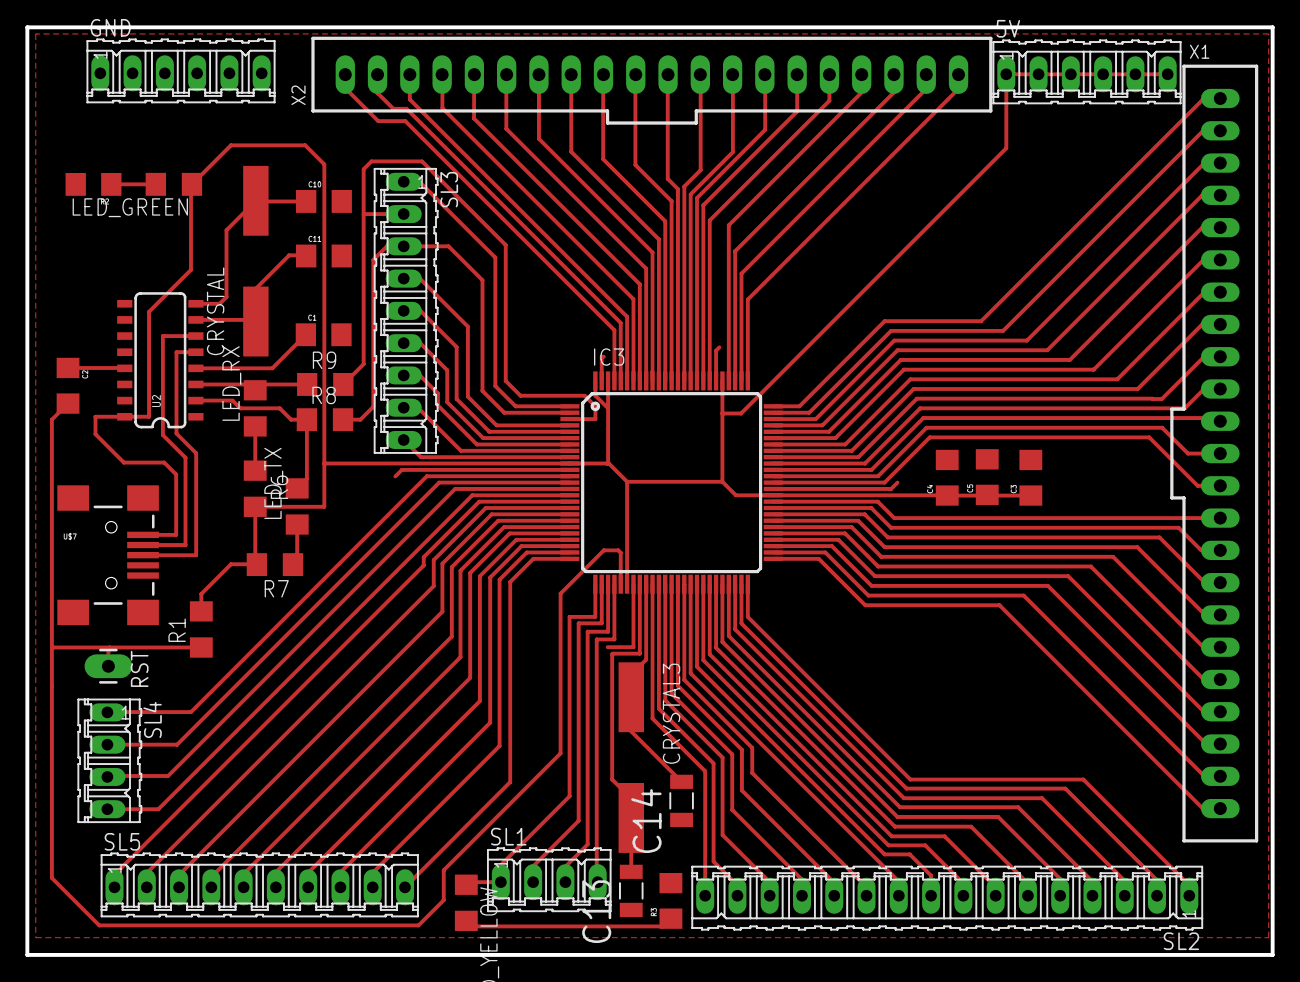
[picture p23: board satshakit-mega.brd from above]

Board: 2 copper layers, 98.0 x 73.0 mm, 35 parts (0 on the bottom side), 103 nets.

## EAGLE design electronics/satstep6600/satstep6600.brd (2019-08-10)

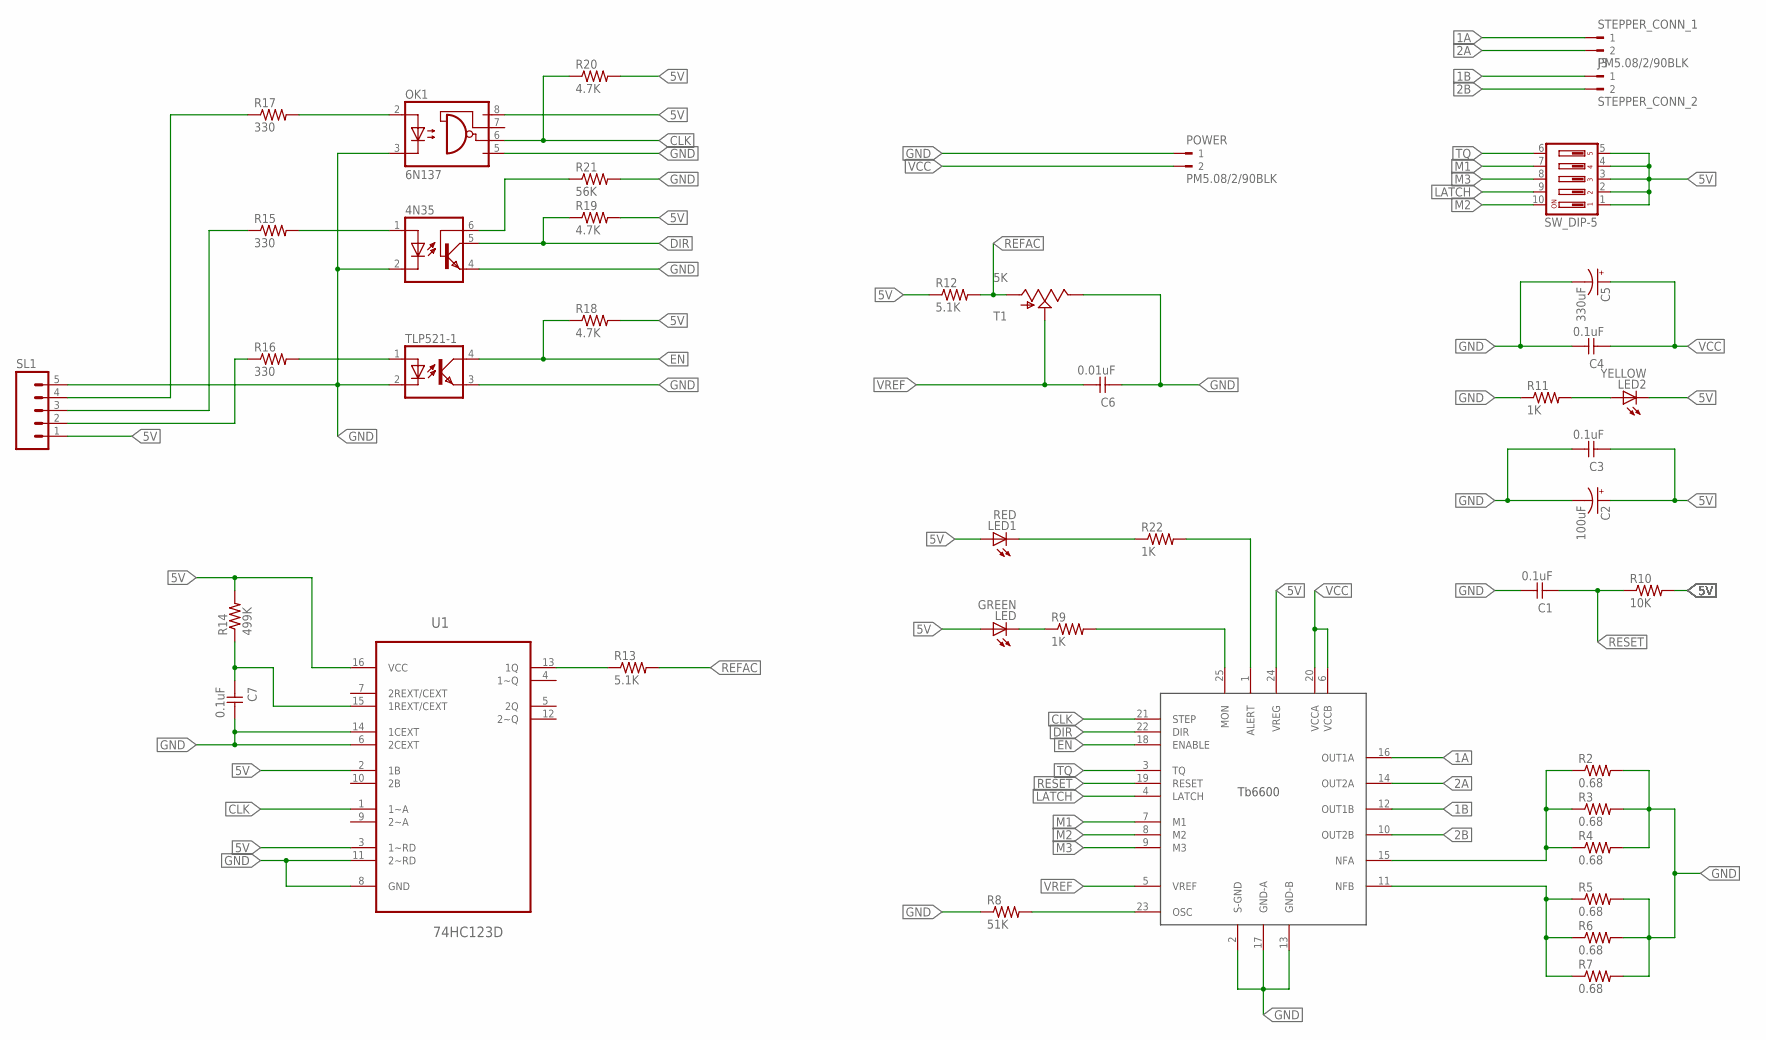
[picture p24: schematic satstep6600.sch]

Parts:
4N35: 4N35; DIL06
C1, C3, C4, C7: 0.1uF; 1206
C2: 100uF; PANASONIC_C
C5: 330uF; CPOL-RADIAL-1000UF-63V
C6: 0.01uF; 1206
J3: STEPPER_CONN_2; WEIDMULLER_PM5.08_2
LED: GREEN; 1206
LED1: RED; 1206
LED2: YELLOW; 1206
OK1: 6N137; DIL08
POWER: PM5.08/2/90BLK; WEIDMULLER_PM5.08_2
R2, R3, R4, R5, R6, R7: 0.68; 2512
R8: 51K; R1206
R9, R11, R22: 1K; R1206
R10: 10K; R1206
R12, R13: 5.1K; R1206
R14: 499K; R1206
R15, R16, R17: 330; R1206
R18, R19, R20: 4.7K; R1206
R21: 56K; R1206
SL1: M05; 05P
STEPPER_CONN_1: PM5.08/2/90BLK; WEIDMULLER_PM5.08_2
SW_DIP-5: SD4-05
T1: 5K; TS53YL104MR10_TRIMMER
TLP521-1: PC817; DIL04
U1: 74HC123D; SOIC127P600X175-16N
U$1: TB6600HG; P-HZIP25-1.00G

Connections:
1A: STEPPER_CONN_1.1, U$1.16 (OUT1A)
1B: J3.1, U$1.12 (OUT1B)
2A: STEPPER_CONN_1.2, U$1.14 (OUT2A)
2B: J3.2, U$1.10 (OUT2B)
5V: C2.+, C3.1, LED.1 (A), LED1.1 (A), LED2.2 (C), OK1.8 (VCC), R10.2, R12.1, R14.2, R18.2, R19.2, R20.2, SL1.1, SW_DIP-5.1, SW_DIP-5.2, SW_DIP-5.3, SW_DIP-5.4, SW_DIP-5.5, U1.2 (1B), U1.3 (1~RD), U1.16 (VCC), U$1.24 (VREG)
ALERT: R22.2, U$1.1 (ALERT)
CLK: OK1.6 (VO), R20.1, U1.1 (1~A), U$1.21 (STEP)
DIR: 4N35.5 (COL), R19.1, U$1.22 (DIR)
EN: R18.1, TLP521-1.4 (COL), U$1.18 (ENABLE)
GND: 4N35.2 (C), 4N35.4 (EMI), C1.2, C2.-, C3.2, C4.2, C5.2 (-), C6.1, C7.2, OK1.3 (C), OK1.5 (GND), POWER.1, R2.2, R3.2, R4.2, R5.2, R6.2, R7.2, R8.1, R11.1, R21.2, SL1.5, T1.P$2 (E), TLP521-1.2 (C), TLP521-1.3 (EMIT), U1.6 (2CEXT), U1.8 (GND), U1.11 (2~RD), U1.14 (1CEXT), U$1.2 (S-GND), U$1.13 (GND-B), U$1.17 (GND-A)
LATCH: SW_DIP-5.9, U$1.4 (LATCH)
M1: SW_DIP-5.7, U$1.7 (M1)
M2: SW_DIP-5.10, U$1.8 (M2)
M3: SW_DIP-5.8, U$1.9 (M3)
unnamed: R5.1, R6.1, R7.1, U$1.11 (NFB)
unnamed: R8.2, U$1.23 (OSC)
unnamed: LED.2 (C), R9.1
unnamed: R2.1, R3.1, R4.1, U$1.15 (NFA)
unnamed: LED1.2 (C), R22.1
unnamed: LED2.1 (A), R11.2
unnamed: R13.1, U1.13 (1Q)
unnamed: C7.1, R14.1, U1.15 (1REXT/CEXT)
unnamed: R16.2, TLP521-1.1 (A)
unnamed: 4N35.1 (A), R15.2
unnamed: OK1.2 (A), R17.2
unnamed: 4N35.6 (BAS), R21.1
unnamed: R16.1, SL1.2
unnamed: R15.1, SL1.3
unnamed: R17.1, SL1.4
unnamed: R9.2, U$1.25 (MON)
REFAC: R12.2, R13.2, T1.P$3 (A)
RESET: C1.1, R10.1, U$1.19 (RESET)
TQ: SW_DIP-5.6, U$1.3 (TQ)
VCC: C4.1, C5.1 (+), POWER.2, U$1.6 (VCCB), U$1.20 (VCCA)
VREF: C6.2, T1.P$1 (S), U$1.5 (VREF)

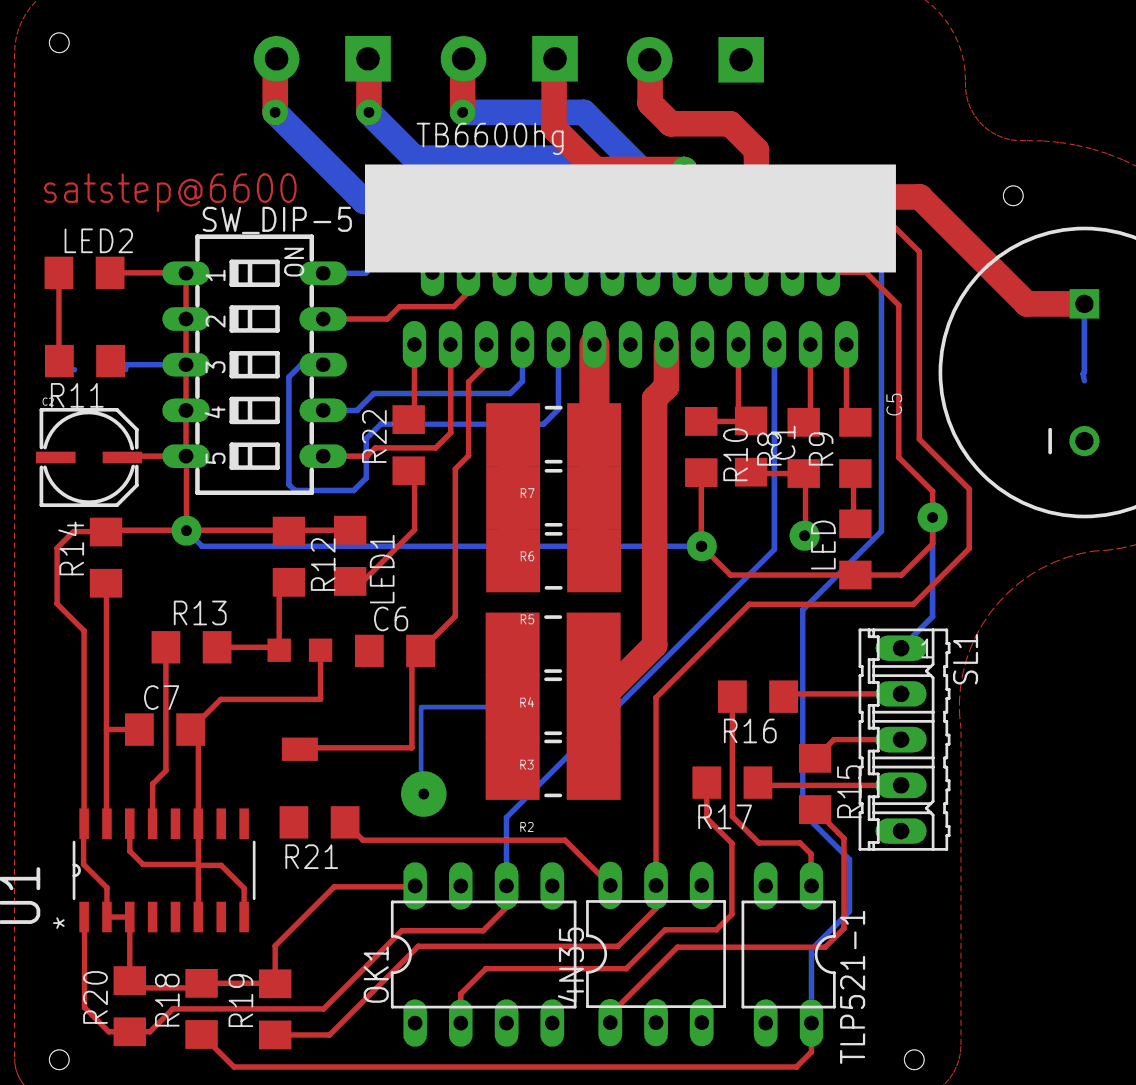
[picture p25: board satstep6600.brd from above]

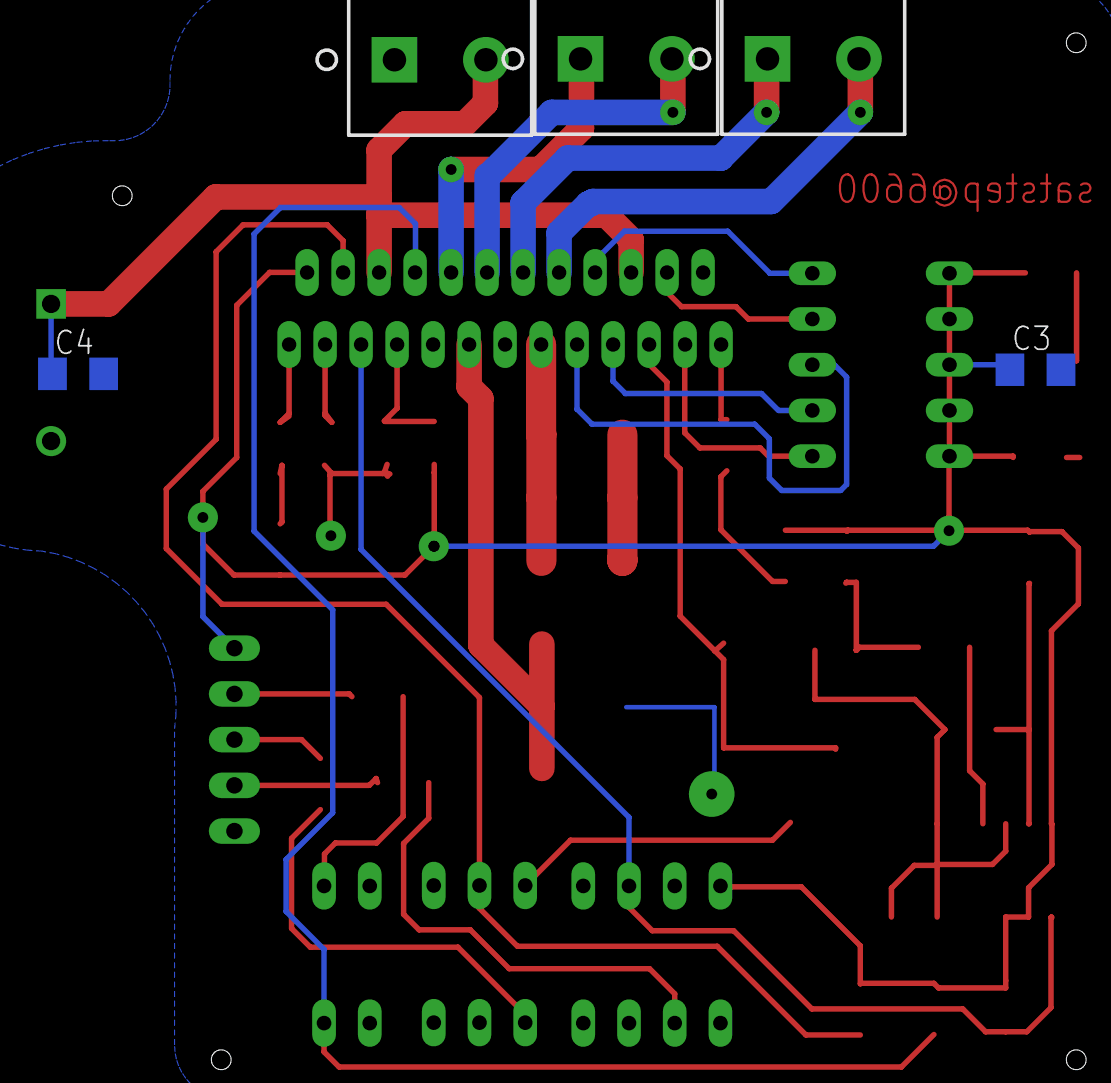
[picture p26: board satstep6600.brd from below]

Board: 2 copper layers, 42 parts (5 on the bottom side), 35 nets.

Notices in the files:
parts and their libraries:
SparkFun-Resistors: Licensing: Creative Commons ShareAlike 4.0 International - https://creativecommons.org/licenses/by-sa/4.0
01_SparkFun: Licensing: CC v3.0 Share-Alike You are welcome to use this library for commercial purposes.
